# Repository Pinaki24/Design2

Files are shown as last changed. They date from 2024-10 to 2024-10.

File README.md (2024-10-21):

# Welcome to the Design 2 Drone Project by Team 02! 😊

This repository contains the source code for implementing key drone functionalities, including:

- **Line Detection**
- **Autonomous Takeoff**
- **Hovering**
- **Landing**

## Features

- **Line Detection**: Detects and follows lines using the ESP32 CAM with MAVLink integration.
- **Autonomous Takeoff**: Enables the drone to take off automatically without manual intervention.
- **Hovering**: Utilizes an optical flow sensor for stable and controlled hovering.
- **Landing**: Automated landing sequence initiated after hovering.

## Technology Stack

- **DroneKit** for flight control
- **MAVLink** for communication with the flight controller
- **ESP32 CAM** for vision-based line detection
- **Optical Flow and LIDAR Sensor** for hover stability
- **PI Control** for motor efficiency
- **HC-SR04 Ultrasonic sensor for obstacle avoidance
- ** ESP to Wifi, creates access point for user 

# Design Output folder
1. Datasheets
2. Documents
3. Test Results
4. Firmware
5. 3D Modelling

## Getting Started

To clone the repository:

```bash
git clone https://github.com/Pinaki24/Design2.git
```
Installing dependencies
```bash
pip install dronekit
pip install dronekit-sitl
```

## Installing Python 3.6.8

For **Windows**, download and install Python 3.6.8 from the [official Python website](https://www.python.org/ftp/python/3.6.8/python-3.6.8-amd64.exe).

Dronekit API requires Python 3.6.8 or Lower,
for more information on DroneKit, visit the [DroneKit GitHub repository](https://github.com/dronekit/dronekit-python).

# Additional libraries:

```bash
pip install opencv-python
pip install numpy
```

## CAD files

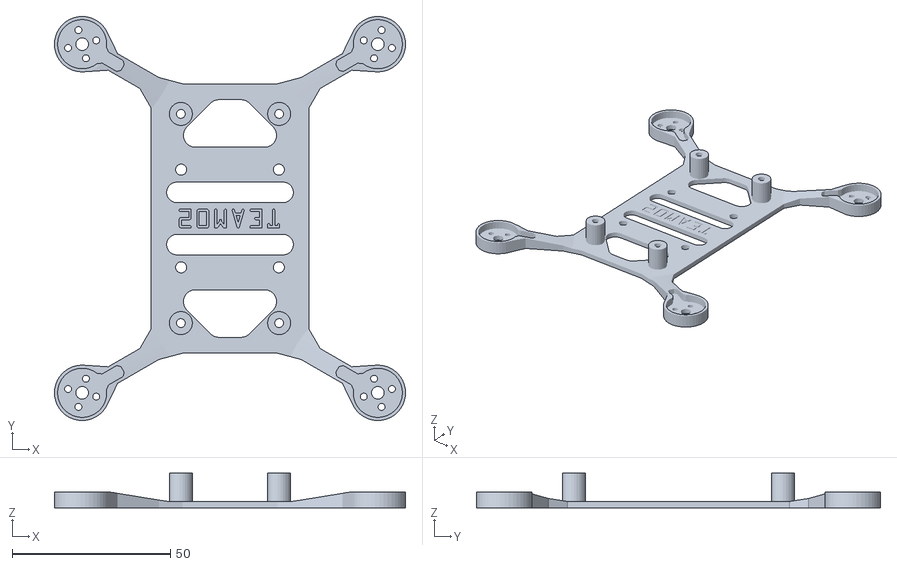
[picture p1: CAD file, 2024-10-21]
Design_outputs_Team02/05. 3D Modelling/01. STLs for 3D Printing/Main body v50.stl
110.8 x 127.5 x 11.0

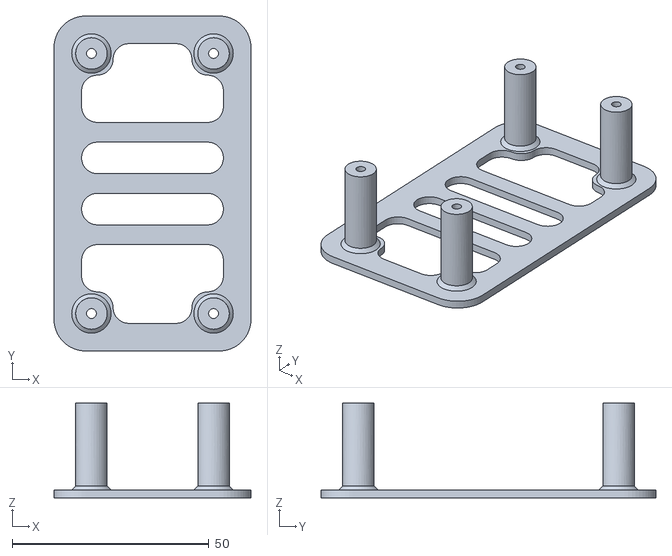
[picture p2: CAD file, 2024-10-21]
Design_outputs_Team02/05. 3D Modelling/01. STLs for 3D Printing/Landing Struts v34.stl
50.0 x 85.0 x 24.0

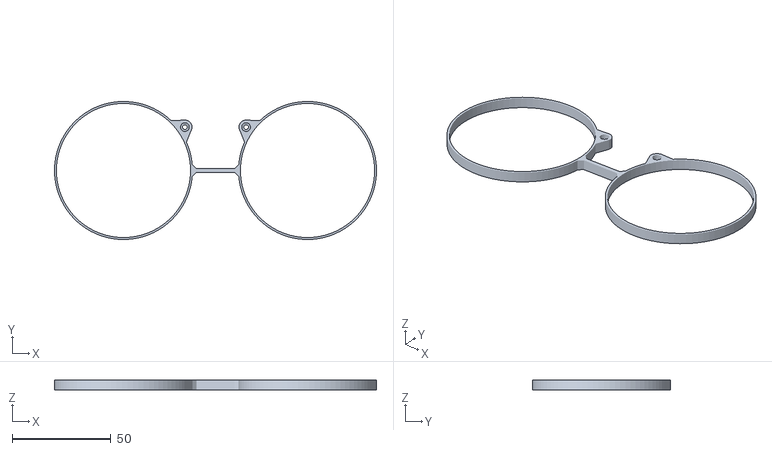
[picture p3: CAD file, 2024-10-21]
Design_outputs_Team02/05. 3D Modelling/01. STLs for 3D Printing/Prop Guard Back v17.stl
163.3 x 70.0 x 5.00

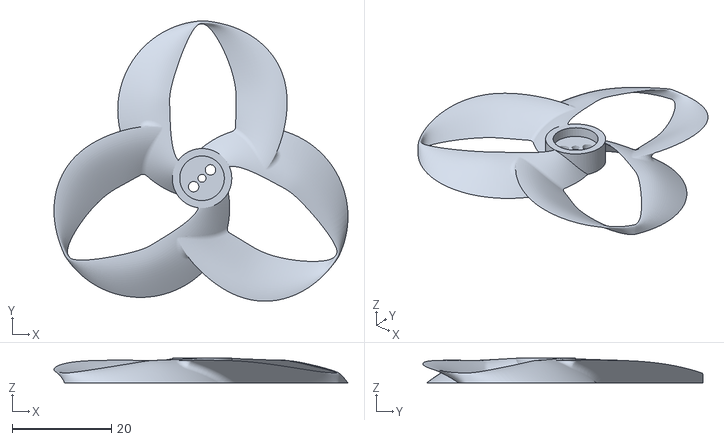
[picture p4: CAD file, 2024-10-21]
Design_outputs_Team02/05. 3D Modelling/01. STLs for 3D Printing/Toroidal Propellor 2-Inch v14.stl
59.3 x 56.5 x 5.00

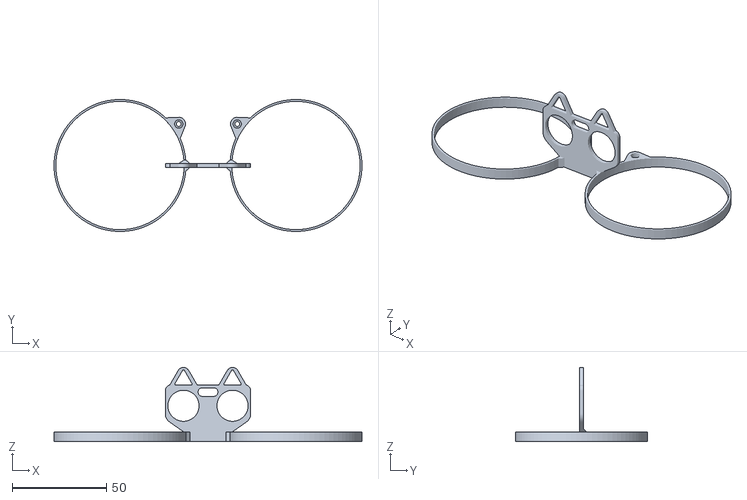
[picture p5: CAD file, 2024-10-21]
Design_outputs_Team02/05. 3D Modelling/01. STLs for 3D Printing/Prop Guard Front v35.stl
163.3 x 69.9 x 39.3

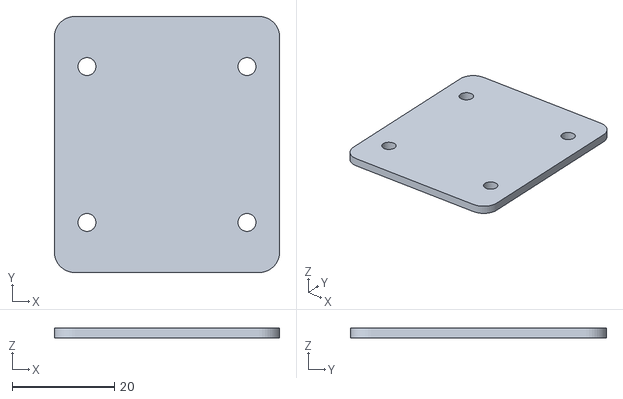
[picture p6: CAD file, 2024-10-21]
Design_outputs_Team02/05. 3D Modelling/01. STLs for 3D Printing/Mounting Plate v4.stl
44.0 x 50.0 x 2.00

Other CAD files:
Design_outputs_Team02/05. 3D Modelling/00. Fusion 360 Files/Landing Struts v34.f3d
Design_outputs_Team02/05. 3D Modelling/00. Fusion 360 Files/Main body v50.f3d
Design_outputs_Team02/05. 3D Modelling/00. Fusion 360 Files/Mounting Plate v3.f3d
Design_outputs_Team02/05. 3D Modelling/00. Fusion 360 Files/Prop Guard Back v17.f3d
Design_outputs_Team02/05. 3D Modelling/00. Fusion 360 Files/Prop Guard Front v35.f3d
Design_outputs_Team02/05. 3D Modelling/00. Fusion 360 Files/Toroidal Propellor 2-Inch v14.f3d

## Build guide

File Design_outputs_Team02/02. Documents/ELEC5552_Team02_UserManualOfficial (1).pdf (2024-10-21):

ELEC5552 | User Manual | Team02
Page | 1

# User Manual

## Autonomous Indoor Line-Following Drone

## Team02

Pinaki Chaturvedi (22485914) Vivian Doan (22978079)
Mathew Jojo (22717226)
Jayden Leveridge-Smith (22274262) Jordon Long (22979549)
Julia Yip (22887946)

## Project Partners

UWA Aviation Labs (UWAAL)
Australian National Fabrication Facility (ANFF)

## Supervised by

Dilusha De Silva

Practical Class

Tuesday, 10-11am

Page | 2

Contents

Page | 3

### 1. Safety Statement

The operator must contact their supervisor should they have any questions regarding this document and must not progress further and only operate the drone in the Lycopodium laboratory.

Under the Civil Aviation Safety Authority's (CASA) rules regarding microdones, the drone must not be operated within 30 meters of another who is not part of the project. The operator must strictly adhere to the no-fly zones around government buildings such as hospitals, airports, national parks and police stations.

### 1.1. Competency Requirements

This document is intended for an operator with at least a bachelor’s degree in engineering or an equivalent licence. The operator must have sufficient computer skills, programming skills and a basic understanding of electrical systems. The operator must complete UWA Non-Staff Safety and Health Induction and Lycopodium Site-Specific Induction. The operator must complete all required documentation and obtain access to the Lycopodium laboratory.

### 1.2. Potential Hazards

Hazards | Cautionary Actions
Electrocution | Exposed wires must not be touched when system is powered. Do not touch leads of electronic speed controller capacitor as it may retain significant charge after use.
Flammable | Battery must be charged following appropriate instructions and stored in LiPo safe bag. Battery should never be disassembled or undergo physical impact. Hazardous substance handling training is required before use.
Slip, Trip, Fall | Keep the workspace clear of obstructions. Ensure cables, wires and tools are correctly stored.
Entanglement | Propellors must never be spun when long hair, jewellery or other loose clothing / accessories are present. Never insert anything including tools or fingers into propellors when they are spinning.
Flying Objects | Drone must always be tightly assembled before flight All fragile objects and unnecessary personnel must be removed from flight area before take-off
High Noise Level | Wear hearing protection when in close vicinity with the drone in operating state.

Page | 4

### 1.3. PPE

Safety Glasses | Gloves | Long Sleeve Clothes | Hearing Protection

### 1.4. Equipment

See Table 1 for the list of equipment that is essential in performing successful operations and Maintenance Activities.

Table 1: Required Equipment to perform Operation and Maintenance Activities

Equipment | Quantity
Laptop with Windows 7 or newer | 1
USB C cable supporting power and data transfer | 1
Multimeter with test probes | 1
M3 Bolts x 16mm Hex Head Style | 4
M2 Bolts x 16mm Phillips Head Style | 4
Breadboard Wires – Male to Male Ends | 2
5V Phone Charger or Equivalent supporting USB Type A | 1

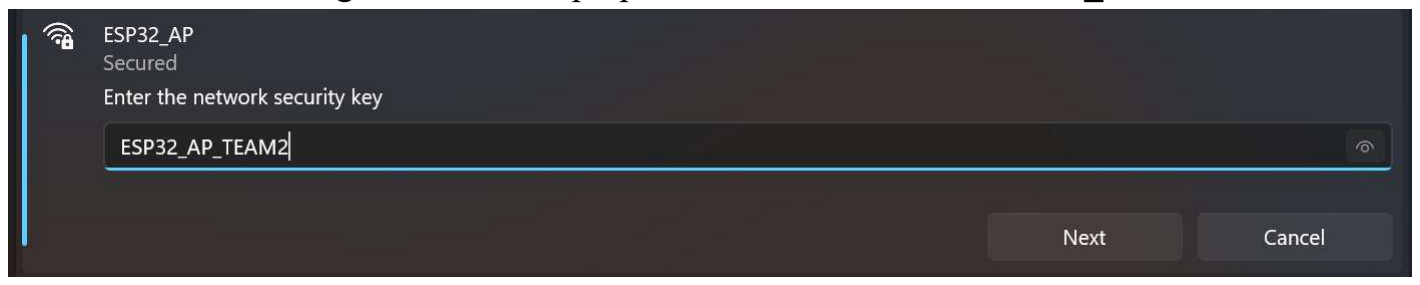
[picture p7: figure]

Page | 5

### 2. Installation Manual

This manual will guide the user through the necessary set-up, operation and maintenance of the drone. The drone uses a custom Python script to control the drone, utilising Dronekit and curses library.

### 2.1. System Requirements:

### 1. Drone Hardware: a MAVLink-compatible Drone 2. Software: Python 2.7 or below installed on a laptop with a keyboard that is able to

connect to the drone via USB or WIFI.
3. Additional Requirements: Dronekit and curses library installed on the laptop.

### 3. Setup:

Flight Controller Setup:

1. First, ensure that Mission Planner is installed. To install Mission Planner, click on the following link and follow the on-screen instructions to complete the installation: https://ardupilot.org/planner/docs/mission-planner-installation.html

Library Installation:

### 1. Ensure that Python is installed on your control laptop. If not installed, click on the

following link and download a Python version 2.7 or later : https://www.python.org/downloads/

### 2. Once Python is downloaded, open the command prompt or terminal on the laptop and

install the necessary Python libraries. Type the following command to do this:

Connection to Drone:

1. Go to the Wi-Fi settings of the user laptop and connect to WIFI “ESP32_AP”.
2. Enter password “ESP32_AP_TEAM2” to connect to the drone.

Page | 6

### 4. Operating Manual

### 4.1. Pre-Flight Checklist:

### 1. Battery Check: Ensure that the battery is fully charged and secured to the drone body

before flight.

### 2. Propellor check: Check that the propellors are secured to the drone frame properly

and that the propellor guards are screwed on.

### 3. Safety Check: Ensure that the operating area is clear of any obstacles that could pose

any danger and that conditions are suitable for flying.

### 4.2. Operating Instructions:

Uploading Python script to Flight Controller:

1. First ensure that the laptop is connected to the ESP32_AP Wi-Fi.

### 2. Ensure that the code includes the following in its connection string:

- UDP connection
- Port configuration is set to 14550 to listen for incoming MAVLink messages
- Wi-Fi IP address is 192.168.4.1

The following should be pre-implemented in the Python script but is mentioned as a precaution.

Take-off:

1. Ensure that the drone is on a flat surface before taking off. Run the script. This will arm the drone and switch it into “GUIDED” mode for manual control flight.

Flight Commands:

- Movement Controls: Use the keyboard keys (W, A, S, D, ) to control the drone’s movement.
- Altitude Control: Use the up and down keys
- Yaw Controls: Use the Left and Right Arrow keys to adjust the drone’s yaw.
- Landing: Press the “L” key to initiate landing. Please note that the user shall observe the surroundings and confirm it is safe for landing before initiating the landing.

### 5. Safeguards:

Communications Failure:

During flight, if the Flight controller Wi-Fi fails to connect to the laptop, the drone is automatically programmed to land the drone if communications is lost for 30 seconds.

Page | 7

### 6. Maintenance Manual

### 6.1. Post-Flight Inspection

After each flight the drone should be inspected to ensure its condition matches that displayed in Figure 1. The following checks should be performed:

1. 4 M3 bolts must be secured in each corner of the mounting plate.
2. 4 M2 bolts must be secured in each corner of the main body such that they are. inserted from the top of the propellor guards, go through the main body and screw into the top of the landing strut.
3. Each propellor should be secured to a motor using 2 of the supplied motor bolts.

### 4. The battery should be securely attached to the top of the mounting plate using the

attached Velcro strip.
5. The obstacle avoidance sensor should be securely attached to in its holder on the front propellor guard.

### 6. All 3D printed parts should be without breakage or deformation. Otherwise, see

section 4.3 on repairing the frame.
7. No wires should be loose and disconnected. Secure loose wires before next take-off. Reconnect unplugged wires where appropriate,

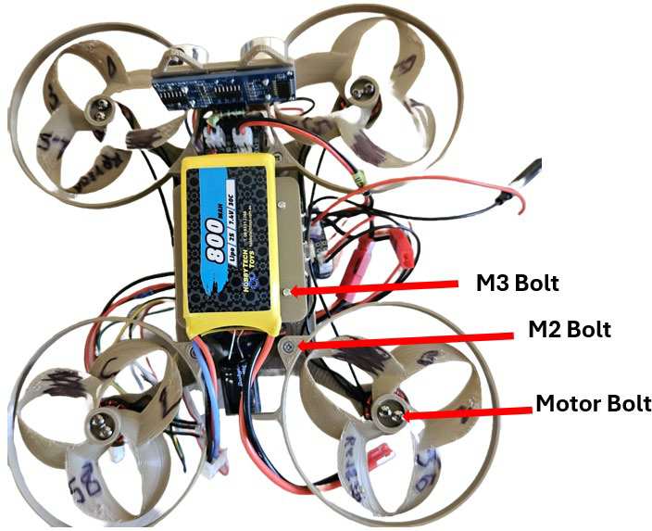
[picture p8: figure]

Figure 1: Assembled Drone Without Damage

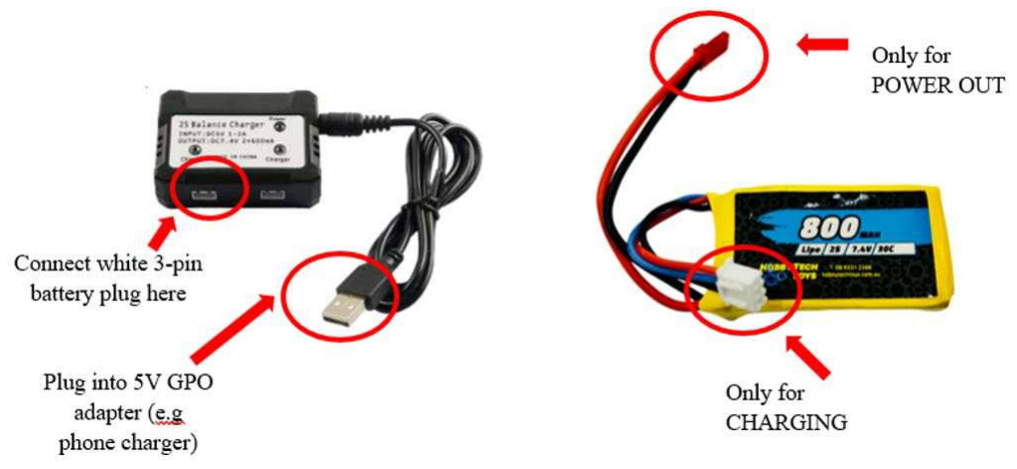
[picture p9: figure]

Page | 8

### 6.2. Battery Maintenance

Precautions

- Do not over-discharge the battery under 3.5V or overcharge the battery above 7.5V.
- The battery will drain within 3 minutes of continuous use with the motors running.
- The LEDs on the charger don’t work properly. Please ignore them.
- If the battery swells and does not cool down within 15 mins after use:

DISCONTINUE USE IMMEDIATELY. Place the battery in a LiPo safe bag and dispose of it according to local council battery disposal laws.

Charging Procedure:

Please refer to Figure 2 regarding the following charging procedure:

### 1. Connect a male-to-male breadboard wire in the positive output of the battery’s red

connector. Do likewise with a separate breadboard wire for the negative output.
2. Ensure multimeter is set to measure voltage and probes are plugged in correctly.

### 3. Use the multimeter to measure the battery voltage by touching the black probe to the

exposed end of the breadboard wire coming from the negative battery output. Do likewise with the red multimeter probe for the positive battery output.
4. If the measured voltage is under 7.3V then the battery requires charging.
5. Plug battery charger into any standard 5V phone charger or similar.
6. Plug 3 pin battery connector into charger.

### 7. Check the battery voltage every 15-30 mins and only do another 15-30 mins if more

charge is needed by re-measuring the batter voltage with the multimeter as per steps 2-4.

Figure 2: The charger (LEFT). The Battery (RIGHT)

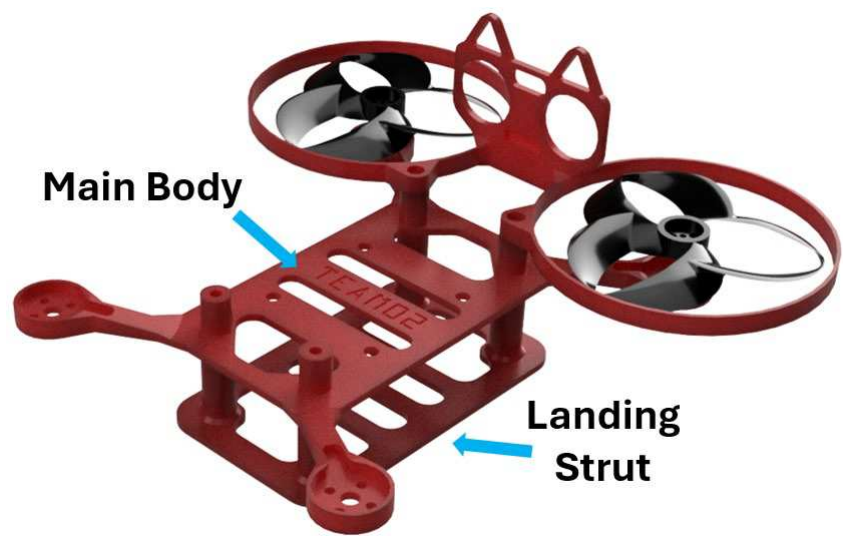
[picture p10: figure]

Page | 9

### 6.3. Frame Repair

All parts of the frame are 3D printed, except for the bolts and threaded inserts. If a piece of the frame breaks the steps to take are as follows:

### 1. Identify the broken piece as per Figure 3.The descriptions in Figure 3 match the

names of the Fusion 360 and STL files corresponding to each piece. These files are in 05.3D Modelling\00. Fusion 360 Files (https://uniwa.sharepoint.com/:f:/r/teams/ELEC5552SEM-22024-Team02/Shared%20Documents/Team02/00.%20Submissions/5.%20Final%20Report%2018-10-2024/Design_outputs/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) and 05.3D Modelling\01.STLs for 3D Printing (https://uniwa.sharepoint.com/:f:/r/teams/ELEC5552SEM-22024-Team02/Shared%20Documents/Team02/00.%20Submissions/5.%20Final%20Report%2018-10-2024/Design_outputs/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) of the design outputs folder respectively.

### 2. Use the Fusion 360 files if the parts need to be altered. New STL files can then be

exported from Fusion 360. Use the STL files if needing to 3D print a replacement.

### 3. To 3D print a new part, upload the relevant STL to any slicing software compatible

with the 3D printer being used. The parts can be printed on any standard FDM 3D printer.
4. Use the slicer, as per the software distributor’s instructions, to slice the desired STL file into gcode.

### 5. Upload the gcode to an appropriate FDM 3D printer and initalise the print as per the

3D printer manufacturer’s instructions.

### 6. Once the required part has been printed, remove from the 3D printer build plate and

remove support structures if necessary. If printing each piece flat, then no supports should be necessary to add.
7. If the part being replaced is the landing strut, then a M2 threaded heat insert will need to be added at the top of each of the 4 landing strut pillars.

### 8. Threaded inserts can be applied by placing heat inserts carefully onto the end of a

soldering iron and then setting the iron to 150°C. Once hot, the inserts can be pressed

gently into the required spot on the frame.

### 9. Once all parts have cooled to room temperature, they are ready to be attached to the

overall drone.

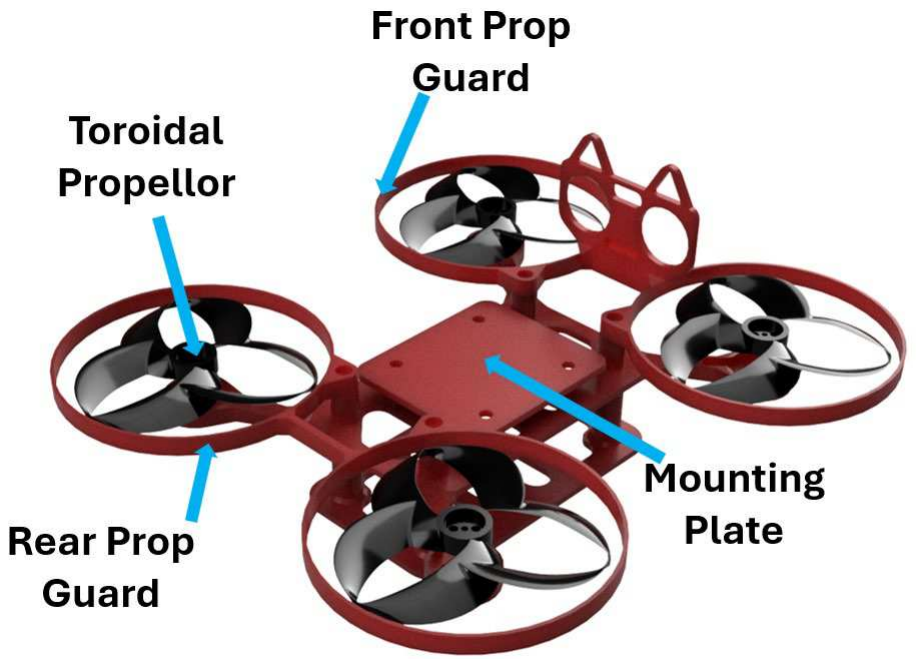
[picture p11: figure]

(A) (B)
Figure 3: (A) Assembled Frame. (B) Frame with Mounting Plate and Rear Components Removed

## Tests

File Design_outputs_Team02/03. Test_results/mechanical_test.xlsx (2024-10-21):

weight on two arms (cup+dirt) | Body Angle | Arm Angle | Permanently deformed
20 | 0 | 0 | 0 | weight of cup (grams) | 10
40 | 2 | 1 | 0
60 | 4 | 5 | 0
80 | 7 | 6 | 0
100 | 10 | 7.5 | 0
120 | 12 | 9 | 0
140 | 13 | 10.4 | 0
160 | 15.4 | 11.3 | 0
180 | 16.1 | 11.5 | 0
200 | 18.6 | 14.4 | 0
220 | 21.1 | 16.2 | 0
240 | 22.2 | 16.2 | 0
260 | 24.2 | 17.4 | 0
280 | 24.6 | 17.6 | 0
300 | 26.7 | 22.1 | 0
320 | 27.3 | 22.7 | 0
380 | 29.4 | 23.3 | 0

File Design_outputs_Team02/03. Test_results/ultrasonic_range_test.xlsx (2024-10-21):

True Distance (cm) | Sample no. | 10.00 | 15.00 | 20.00 | 25.00 | 30.00 | 35.00 | 40.00 | 45.00 | 50.00 | 55.00 | 60.00 | 65.00 | 70.00 | 75.00 | 80.00 | 85.00 | 90.00 | 95.00 | 100.00
Recorded Distance (cm) | 1 | 9.10 | 14.35 | 21.51 | 25.94 | 31.00 | 35.01 | 40.68 | 46.07 | 50.66 | 55.21 | 60.71 | 65.34 | 69.54 | 75.06 | 80.93 | 84.64 | 90.59 | 94.07 | 99.66
 | 2 | 9.11 | 14.28 | 21.52 | 26.03 | 30.79 | 35.01 | 40.72 | 46.03 | 50.72 | 55.07 | 60.74 | 65.36 | 69.81 | 75.05 | 80.92 | 84.87 | 90.59 | 94.10 | 100.13
 | 3 | 9.03 | 14.21 | 21.55 | 26.05 | 30.62 | 35.01 | 40.70 | 45.99 | 50.78 | 55.02 | 60.74 | 65.40 | 69.74 | 75.10 | 80.92 | 85.02 | 90.62 | 94.23 | 100.60
 | 4 | 8.94 | 14.21 | 21.42 | 26.03 | 30.47 | 35.01 | 40.67 | 45.92 | 50.84 | 54.90 | 60.76 | 65.43 | 69.92 | 75.05 | 80.93 | 85.02 | 90.68 | 94.42 | 101.00
 | 5 | 9.02 | 14.23 | 21.42 | 26.15 | 30.30 | 35.03 | 40.62 | 45.83 | 50.86 | 54.76 | 60.76 | 65.48 | 69.97 | 75.00 | 80.93 | 85.14 | 90.68 | 95.08 | 101.41
 | 6 | 9.05 | 14.19 | 21.45 | 26.06 | 30.14 | 35.03 | 40.59 | 45.78 | 50.92 | 54.63 | 60.76 | 65.51 | 70.01 | 74.95 | 80.88 | 85.32 | 90.68 | 95.23 | 101.47
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

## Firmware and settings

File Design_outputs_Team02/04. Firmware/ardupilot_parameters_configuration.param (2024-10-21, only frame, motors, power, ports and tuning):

ATC_ANG_LIM_TC,1
ATC_ANG_PIT_P,4.5
ATC_ANG_RLL_P,4.5
ATC_ANG_YAW_P,4.5
ATC_ANGLE_BOOST,1
ATC_RAT_PIT_D,0.0036
ATC_RAT_PIT_D_FF,0
ATC_RAT_PIT_FF,0
ATC_RAT_PIT_FLTD,81
ATC_RAT_PIT_FLTE,0
ATC_RAT_PIT_FLTT,81
ATC_RAT_PIT_I,0.135
ATC_RAT_PIT_IMAX,0.5
ATC_RAT_PIT_P,0.135
ATC_RAT_PIT_PDMX,0
ATC_RAT_PIT_SMAX,0
ATC_RAT_RLL_D,0.0036
ATC_RAT_RLL_D_FF,0
ATC_RAT_RLL_FF,0
ATC_RAT_RLL_FLTD,81
ATC_RAT_RLL_FLTE,0
ATC_RAT_RLL_FLTT,81
ATC_RAT_RLL_I,0.135
ATC_RAT_RLL_IMAX,0.5
ATC_RAT_RLL_P,0.135
ATC_RAT_RLL_PDMX,0
ATC_RAT_RLL_SMAX,0
ATC_RAT_YAW_D,0
ATC_RAT_YAW_D_FF,0
ATC_RAT_YAW_FF,0
ATC_RAT_YAW_FLTD,0
ATC_RAT_YAW_FLTE,2
ATC_RAT_YAW_FLTT,81
ATC_RAT_YAW_I,0.018
ATC_RAT_YAW_IMAX,0.5
ATC_RAT_YAW_P,0.18
ATC_RAT_YAW_PDMX,0
ATC_RAT_YAW_SMAX,0
ATC_RATE_FF_ENAB,1
ATC_RATE_P_MAX,0
ATC_RATE_R_MAX,0
ATC_RATE_Y_MAX,0
BATT_AMP_OFFSET,0
BATT_AMP_PERVLT,66.7
BATT_ARM_MAH,0
BATT_ARM_VOLT,7.3
BATT_CAPACITY,800
BATT_CRT_MAH,0
BATT_CRT_VOLT,7
BATT_CURR_PIN,15
BATT_FS_CRT_ACT,0
BATT_FS_LOW_ACT,0
BATT_FS_VOLTSRC,0
BATT_LOW_MAH,0
BATT_LOW_TIMER,10
BATT_LOW_VOLT,7.2
BATT_MONITOR,4
BATT_OPTIONS,0
BATT_SERIAL_NUM,-1
BATT_VLT_OFFSET,0
BATT_VOLT_MULT,11
BATT_VOLT_PIN,15
BATT2_MONITOR,0
BATT3_MONITOR,0
BATT4_MONITOR,0
BATT5_MONITOR,0
BATT6_MONITOR,0
BATT7_MONITOR,0
BATT8_MONITOR,0
BATT9_MONITOR,0
FLTMODE_CH,5
FLTMODE_GCSBLOCK,0
FLTMODE1,0
FLTMODE2,0
FLTMODE3,0
FLTMODE4,0
FLTMODE5,0
FLTMODE6,0
FRAME_CLASS,1
FRAME_TYPE,3
INS_GYRO_FILTER,162
INS_HNTCH_ENABLE,0
MOT_BAT_CURR_MAX,0
MOT_BAT_CURR_TC,5
MOT_BAT_IDX,0
MOT_BAT_VOLT_MAX,15
MOT_BAT_VOLT_MIN,6.6
MOT_BOOST_SCALE,0
MOT_HOVER_LEARN,2
MOT_OPTIONS,0
MOT_PWM_MAX,2000
MOT_PWM_MIN,1000
MOT_PWM_TYPE,6
MOT_SAFE_DISARM,0
MOT_SAFE_TIME,1
MOT_SLEW_DN_TIME,0
MOT_SLEW_UP_TIME,0
MOT_SPIN_ARM,0.1
MOT_SPIN_MAX,0.95
MOT_SPIN_MIN,0.15
MOT_SPOOL_TIM_DN,0
MOT_SPOOL_TIME,0.5
MOT_THST_EXPO,0.35
MOT_THST_HOVER,0.2
MOT_YAW_HEADROOM,200
SERIAL0_BAUD,115
SERIAL0_PROTOCOL,2
SERIAL1_BAUD,921
SERIAL1_OPTIONS,0
SERIAL1_PROTOCOL,2
SERIAL2_BAUD,115
SERIAL2_OPTIONS,0
SERIAL2_PROTOCOL,-1
SERIAL3_BAUD,115
SERIAL3_OPTIONS,0
SERIAL3_PROTOCOL,2
SERIAL4_BAUD,230
SERIAL4_OPTIONS,0
SERIAL4_PROTOCOL,5
SERIAL5_BAUD,115
SERIAL5_OPTIONS,0
SERIAL5_PROTOCOL,32
SERIAL6_BAUD,57
SERIAL6_OPTIONS,0
SERIAL6_PROTOCOL,-1
SERVO1_FUNCTION,-1
SERVO1_MAX,1900
SERVO1_MIN,1100
SERVO1_REVERSED,0
SERVO1_TRIM,1500
SERVO2_FUNCTION,-1
SERVO2_MAX,1900
SERVO2_MIN,1100
SERVO2_REVERSED,0
SERVO2_TRIM,1500
SERVO3_FUNCTION,0
SERVO3_MAX,1900
SERVO3_MIN,1100
SERVO3_REVERSED,0
SERVO3_TRIM,1500
SERVO4_FUNCTION,0
SERVO4_MAX,1900
SERVO4_MIN,1100
SERVO4_REVERSED,0
SERVO4_TRIM,1500
SERVO5_FUNCTION,33
SERVO5_MAX,2000
SERVO5_MIN,1000
SERVO5_REVERSED,1
SERVO5_TRIM,1000
SERVO6_FUNCTION,36
SERVO6_MAX,2000
SERVO6_MIN,1000
SERVO6_REVERSED,0
SERVO6_TRIM,1000
SERVO7_FUNCTION,35
SERVO7_MAX,2000
SERVO7_MIN,1000
SERVO7_REVERSED,1
SERVO7_TRIM,1000
SERVO8_FUNCTION,34
SERVO8_MAX,2000
SERVO8_MIN,1000
SERVO8_REVERSED,1
SERVO8_TRIM,1000
SERVO9_FUNCTION,0
SERVO9_MAX,1900
SERVO9_MIN,1100
SERVO9_REVERSED,0
SERVO9_TRIM,1500

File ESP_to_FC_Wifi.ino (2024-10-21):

#include <WiFi.h>
#include <WebServer.h>
#include "esp_camera.h"
#include "esp32-hal.h" // Include the ESP32 hardware abstraction layer

// Replace with your new network credentials
const char *ssid = "ESP32_AP";    // New WiFi network name (SSID)
const char *password = "ESP32_AP_TEAM2"; // New WiFi password
const char *hostname = "ESP32_QUANTUM"; // Optional hostname for the ESP32

// Create a web server on port 80
WebServer server(80);

// Camera configuration (specific to AI-Thinker ESP32-CAM)
#define CAMERA_MODEL_AI_THINKER
#include "camera_pins.h" // Pin definitions for the AI-Thinker camera

String telemetryData = ""; // Variable to store telemetry data

void startCameraServer(); // Function to start the camera server

void setup() {
  Serial.begin(115200); // Initialize serial communication at 115200 baud rate

  // Set Wi-Fi mode to Access Point
  WiFi.mode(WIFI_AP);
  WiFi.softAP(ssid, password); // Start WiFi in Access Point mode with the provided credentials
  WiFi.setHostname(hostname); // Set the device hostname

  Serial.print("Access Point IP address: ");
  Serial.println(WiFi.softAPIP()); // Print the Access Point IP address

  // Initialize the camera
  camera_config_t config;
  config.ledc_channel = LEDC_CHANNEL_0;
  config.ledc_timer = LEDC_TIMER_0;
  config.pin_d0 = Y2_GPIO_NUM;
  config.pin_d1 = Y3_GPIO_NUM;
  config.pin_d2 = Y4_GPIO_NUM;
  config.pin_d3 = Y5_GPIO_NUM;
  config.pin_d4 = Y6_GPIO_NUM;
  config.pin_d5 = Y7_GPIO_NUM;
  config.pin_d6 = Y8_GPIO_NUM;
  config.pin_d7 = Y9_GPIO_NUM;
  config.pin_xclk = XCLK_GPIO_NUM;
  config.pin_pclk = PCLK_GPIO_NUM;
  config.pin_vsync = VSYNC_GPIO_NUM;
  config.pin_href = HREF_GPIO_NUM;
  config.pin_sscb_sda = SIOD_GPIO_NUM;
  config.pin_sscb_scl = SIOC_GPIO_NUM;
  config.pin_pwdn = PWDN_GPIO_NUM; // Power down pin
  config.pin_reset = RESET_GPIO_NUM; // Reset pin
  config.xclk_freq_hz = 20000000; // XCLK frequency
  config.pixel_format = PIXFORMAT_JPEG; // Use JPEG format for camera output

  // Optional settings to adjust frame size and quality based on PSRAM availability
  if(psramFound()){
    config.frame_size = FRAMESIZE_QVGA; // Set lower resolution (QVGA) for better performance
    config.jpeg_quality = 10; // Set JPEG quality (lower means higher quality)
    config.fb_count = 2; // Use double buffer
  } else {
    config.frame_size = FRAMESIZE_SVGA; // Higher resolution if no PSRAM
    config.jpeg_quality = 12; // Lower JPEG quality for better performance
    config.fb_count = 1; // Single buffer
  }

  // Initialize the camera and check for errors
  esp_err_t err = esp_camera_init(&config);
  if (err != ESP_OK) {
    Serial.printf("Camera init failed with error 0x%x", err);
    return;
  }

  // Adjust camera settings
  sensor_t * s = esp_camera_sensor_get();
  s->set_framesize(s, FRAMESIZE_QVGA); // Set frame size to QVGA
  s->set_quality(s, 10); // Set quality (lower value = better quality)
  s->set_brightness(s, 0); // Default brightness
  s->set_contrast(s, 0); // Default contrast
  s->set_saturation(s, 0); // Default saturation
  s->set_gainceiling(s, (gainceiling_t)0); // Default gain ceiling
  s->set_special_effect(s, 2); // 2 = grayscale effect

  // Start the web server
  startCameraServer();
}

void loop() {
  server.handleClient(); // Handle client requests
  updateTelemetryData(); // Update telemetry data
  if (Serial.available() > 0) {
    telemetryData = Serial.readStringUntil('\n'); // Read telemetry data from serial input
    Serial.println("Received telemetry data: " + telemetryData);
  }
}

void updateTelemetryData() {
  // Example telemetry data (can be modified to read real sensors)
  int sensorValue = 20; // Simulated analog sensor value
  float temperature = InternaltemperatureRead(); // Read internal temperature sensor
  float batteryLevel = 3.7; // Simulated battery level

  // Format telemetry data as a string
  telemetryData = "Sensor Value: " + String(sensorValue) + "\n";
  telemetryData += "Temperature: " + String(temperature) + " C\n";
  telemetryData += "Battery Level: " + String(batteryLevel) + " V\n";
  telemetryData += "Vivian gonna have to learn ESP32 now\n"; // Custom message
}

void handleCameraPage() {
  // HTML page to display the camera stream
  String html = "<html><head><style>body { font-family: Arial, sans-serif; } #cameraImage { width: 640px; height: 480px; }</style></head><body><h1>ESP32 Camera</h1><img src=\"/capture\" id=\"cameraImage\"><script>setInterval(function() {document.getElementById('cameraImage').src = '/capture?rand=' + Math.random();}, 250);</script></body></html>";
  server.send(200, "text/html", html); // Send HTML page
}

void handleTelemetryPage() {
  // HTML page to display telemetry data
  String html = "<html><head><style>";
  html += "body { font-family: Arial, sans-serif; }";
  html += "pre { font-size: 20px; }"; // Style telemetry data
  html += "</style></head><body>";
  html += "<h1>Telemetry Data</h1>";
  html += "<pre id='telemetry'>" + telemetryData + "</pre>";
  html += "<script>setInterval(function() {fetch('/telemetryData').then(response => response.text()).then(data => {document.getElementById('telemetry').innerText = data;});}, 500);</script>";
  html += "</body></html>";
  server.send(200, "text/html", html); // Send HTML page
}

void handleTelemetryData() {
  // Send the current telemetry data as plain text
  updateTelemetryData();
  server.send(200, "text/plain", telemetryData);
}

void handleCapture() {
  // Capture an image from the camera
  camera_fb_t * fb = NULL;
  fb = esp_camera_fb_get(); // Get the camera framebuffer
  if (!fb) {
    Serial.println("Camera capture failed");
    server.send(500, "text/plain", "Camera capture failed");
    return;
  }
  server.send_P(200, "image/jpeg", (const char *)fb->buf, fb->len); // Send the captured image
  esp_camera_fb_return(fb); // Return the framebuffer
}

void handleStream() {
  // Start MJPEG stream
  server.setContentLength(CONTENT_LENGTH_UNKNOWN);
  server.send(200, "multipart/x-mixed-replace; boundary=frame");

  while (server.client().connected()) {  // Check if the client is still connected
    camera_fb_t * fb = esp_camera_fb_get(); // Capture frame buffer
    if (!fb) {
      Serial.println("Camera capture failed");
      break;
    }

    // Send the MJPEG frame
    server.sendContent("--frame\r\n");
    server.sendContent("Content-Type: image/jpeg\r\n\r\n");
    server.sendContent((const char *)fb->buf, fb->len);
    server.sendContent("\r\n");
    esp_camera_fb_return(fb); // Return the frame buffer

    // Add a small delay to avoid overwhelming the client
    delay(100);
  }
}


void startCameraServer() {
  // Set up URL handlers for the web server 
  server.on("/", HTTP_GET, handleCameraPage); // Handle root URL for camera page
  server.on("/telemetry", HTTP_GET, handleTelemetryPage); // Handle telemetry page
  server.on("/telemetryData", HTTP_GET, handleTelemetryData); // Handle telemetry data requests
  server.on("/capture", HTTP_GET, handleCapture); // Handle camera capture requests
  server.on("/stream", HTTP_GET, handleStream); // Handle MJPEG stream requests
  server.begin(); // Start the web server
}

float InternaltemperatureRead() {
  // Read the internal temperature sensor (convert to Celsius)
  return (temperatureRead() - 32) / 1.8; //
}

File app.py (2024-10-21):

import cv2
import numpy as np
import math
import time
from dronekit import connect, VehicleMode, LocationGlobalRelative
from PI import PIController
from Line_detection import detect_line_angle_and_displacement
from pymavlink import mavutil

# Create instances of the PI controllers for angle and displacement
angle_pi_controller = PIController(kp=0.5, ki=0.05, output_limits=(-10, 10))
displacement_pi_controller = PIController(kp=0.3, ki=0.03, output_limits=(-0.5, 0.5))

def send_attitude_target(roll_angle, pitch_angle, yaw_angle, thrust):
    # Replace with actual DroneKit commands to set drone attitude
    print(f"send_attitude_target called with roll_angle={roll_angle}, pitch_angle={pitch_angle}, yaw_angle={yaw_angle}, thrust={thrust}")

def change_velocity(velocity_x, velocity_y, velocity_z):
    # Calculate the new target location based on the velocity vectors
    current_location = vehicle.location.global_relative_frame
    north = velocity_x
    east = velocity_y
    down = -velocity_z  # Negative because 'down' needs to be positive in NED
    target_location = LocationGlobalRelative(current_location.lat + north/1e5, current_location.lon + east/1e5, current_location.alt + down)
    vehicle.simple_goto(target_location)

def initiate_landing():
    vehicle.mode = VehicleMode("LAND")
    while vehicle.armed:
        print("Landing...")
        time.sleep(1)
    print("Landed and disarmed.")

def arm_and_takeoff(aTargetAltitude):
    print("Basic pre-arm checks")
    while not vehicle.is_armable:
        print("Waiting for vehicle to initialise...")
        time.sleep(1)

    print("Arming motors")
    vehicle.mode = VehicleMode("GUIDED")
    vehicle.armed = True

    while not vehicle.armed:
        print("Waiting for arming...")
        time.sleep(1)

    print("Taking off!")
    vehicle.simple_takeoff(aTargetAltitude)

    while True:
        alt = vehicle.location.global_relative_frame.alt
        print(f"Altitude: {alt:.2f}m")
        if alt >= aTargetAltitude * 0.95:
            print("Reached target altitude")
            break
        time.sleep(1)

def main():
    # Connect to the drone via WiFi from ESP32
    global vehicle
    vehicle = connect('COM3', baud=57600, wait_ready=True)

    arm_and_takeoff(3)  # Take off to 3 meters

    vehicle.mode = VehicleMode("GUIDED")
    while vehicle.mode.name != "GUIDED":
        time.sleep(1)
    vehicle.armed = True
    while not vehicle.armed:
        time.sleep(1)
    print("Vehicle armed and in GUIDED mode.")

    # Initialize camera
    cap = cv2.VideoCapture(0)  # Adjust camera index if necessary

    if not cap.isOpened():
        print("Error: Unable to open the camera.")
        vehicle.mode = VehicleMode("LAND")
        vehicle.close()
        return

    try:
        while True:
            ret, frame = cap.read()
            if not ret:
                print("Error: Unable to capture video frame.")
                break

            current_time = time.time()

            # Process the frame and extract line information
            line_angle, line_displacement = detect_line_angle_and_displacement()

            # Update PI controllers
            angle_correction = angle_pi_controller.compute(line_angle, current_time)
            displacement_correction = displacement_pi_controller.compute(line_displacement, current_time)

            # Set desired yaw angle and velocities based on corrections
            yaw_angle = angle_correction
            thrust = 0.5  # Maintaining constant thrust
            velocity_x = 0.5  # Moving forward constantly
            velocity_y = displacement_correction
            velocity_z = 0

            # Send commands to drone to update its position and attitude
            send_attitude_target(roll_angle=0, pitch_angle=0, yaw_angle=yaw_angle, thrust=thrust)
            change_velocity(velocity_x, velocity_y, velocity_z)

            # Print outputs for visualization
            print(f"Angle Controller Output: {yaw_angle:.2f} degrees")
            print(f"Displacement Controller Output: {velocity_y:.2f} units")
            print(f"send_attitude_target called with roll_angle=0, pitch_angle=0, yaw_angle={yaw_angle}, thrust={thrust}")
            print(f"send_velocity called with velocity_x={velocity_x}, velocity_y={velocity_y}, velocity_z={velocity_z}")

            # Display the frame with lines (optional)
            cv2.imshow('Line Detection', frame)
            if cv2.waitKey(1) & 0xFF == ord('q'):
                break

            time.sleep(0.1)  # Control loop delay

    finally:
        # Clean up
        cap.release()
        cv2.destroyAllWindows()
        vehicle.mode = VehicleMode("LAND")
        vehicle.close()

if __name__ == "__main__":
    try:
        main()
    except KeyboardInterrupt:
        print("\nShutting down...")
    finally:
        vehicle.close()

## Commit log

2024-07-27 engergence landing
2024-09-29 GUI installed, PC camera setup
2024-10-10 Connects to drone but doesnt arm
